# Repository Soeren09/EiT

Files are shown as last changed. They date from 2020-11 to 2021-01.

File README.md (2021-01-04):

# EiT
Practial project for Expert in Teams

# Folder structure
```bash
.Root
+-- Device_Tryouts
|   +-- # Contains Scene .xml file and collision setup
|   |
|   +-- components
|       +-- # Contains object files in .stl format
|
+-- PrototypeControl
|   +-- # Robot control
|
+-- STOMPA
|   +-- 3D Print
|   |   +-- # Contains all 3D printed components
|   +-- LaserCut
|   |   +-- # Containt all laser cutter drawings 
|   +-- PDF Work Drawings
|   |   +-- # Containt all Work Drawings for the mechanical components
|   +-- STOMPA 3D files
|       +-- # Containt the Invertor files for the CAD model
| 
+-- Workcell
|   +-- # Examplecode for RobworkStudio scene
|
+-- PluginUIapp
    +-- # Contain code for simulating the STOMPA in RobworkStudio
    
```

To rebuild the pluginUIapp.so:
Local paths are stored in: pluginUIapp/src/AbsolutePaths.h
which is ignored by git so you will have to create it. Mine looks like this:

#ifndef PLUGINUIAPP_ABSOLUTEPATHS_H
#define PLUGINUIAPP_ABSOLUTEPATHS_H
#include <string>

//Malte:
const std::string URFilePath = "/home/maltenj/EiT/Workcell/Scene.wc.xml";
const std::string GantryFilePath = "/home/maltenj/EiT/Device_Tryouts/STOMPAScene.xml";
const std::string PlaybackFilePath = "/home/maltenj/EiT/pluginUIapp/src/";
const char* GoogleLogPath =  "/home/maltenj/EiT/pluginUIapp/src/";

#endif

Insert your own paths. 

Also we linked ceres, so you might have to install it. see http://ceres-solver.org/
Alternatively you can delete all references to it. We don't use it currently. 

To build run:
$ cd /<PathToGit>/Eit/Practical/EiT/pluginUIapp/build
$ cmake ..
$ make -j4

And pray it links correctly...

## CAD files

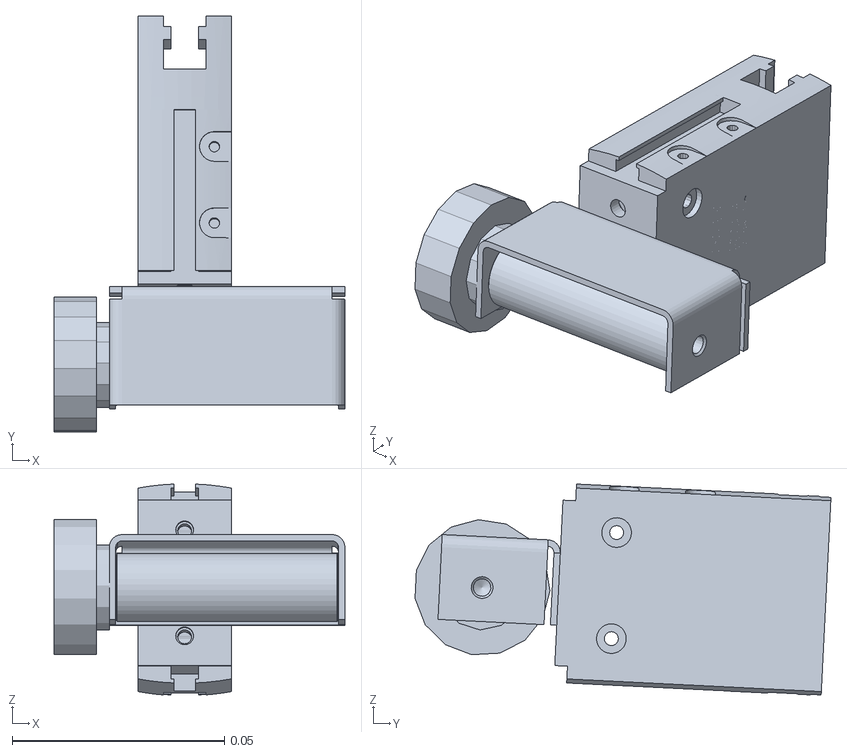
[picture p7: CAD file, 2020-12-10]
Device_Tryouts/components/test.stl
0.0685 x 0.098 x 0.0497

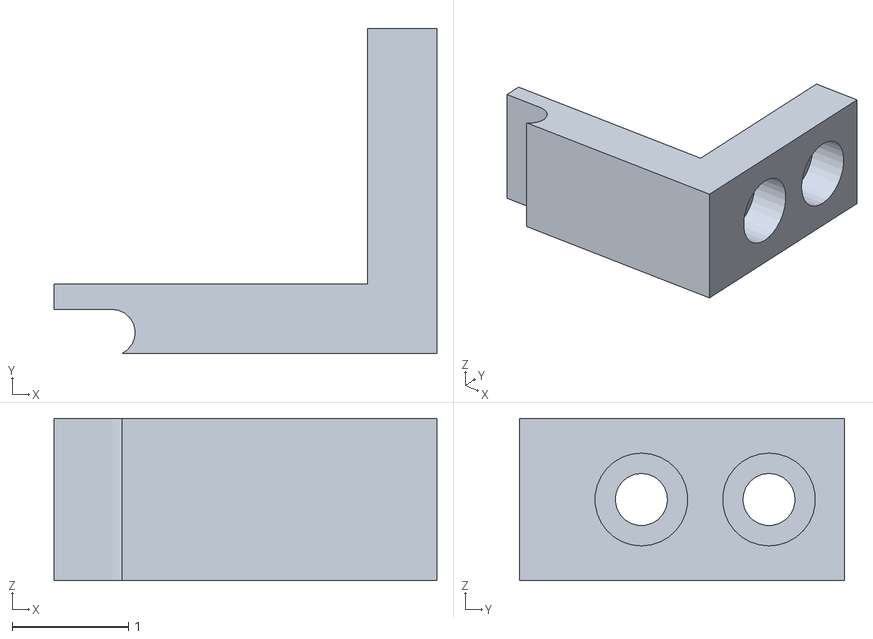
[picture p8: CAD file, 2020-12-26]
STOMPA/3Dprint/Gripper arm_extended2.stl
3.30 x 2.80 x 1.40

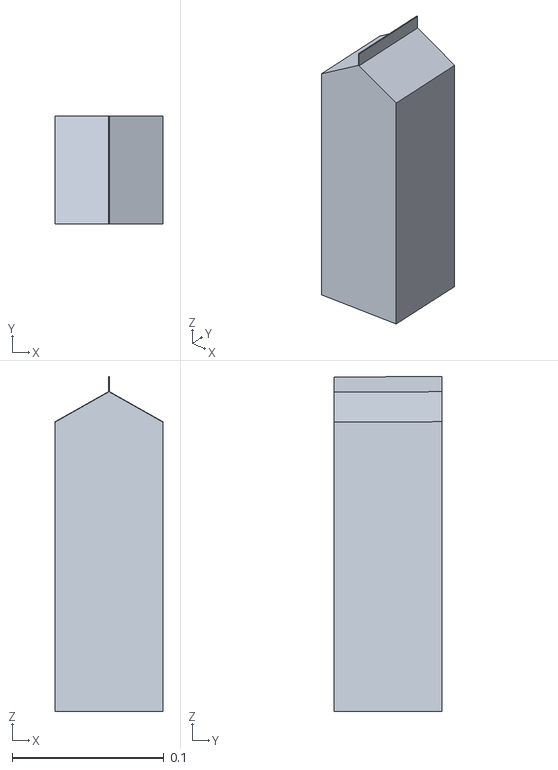
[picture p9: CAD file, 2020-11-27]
Workcell/parts/milk.obj
0.071 x 0.071 x 0.221

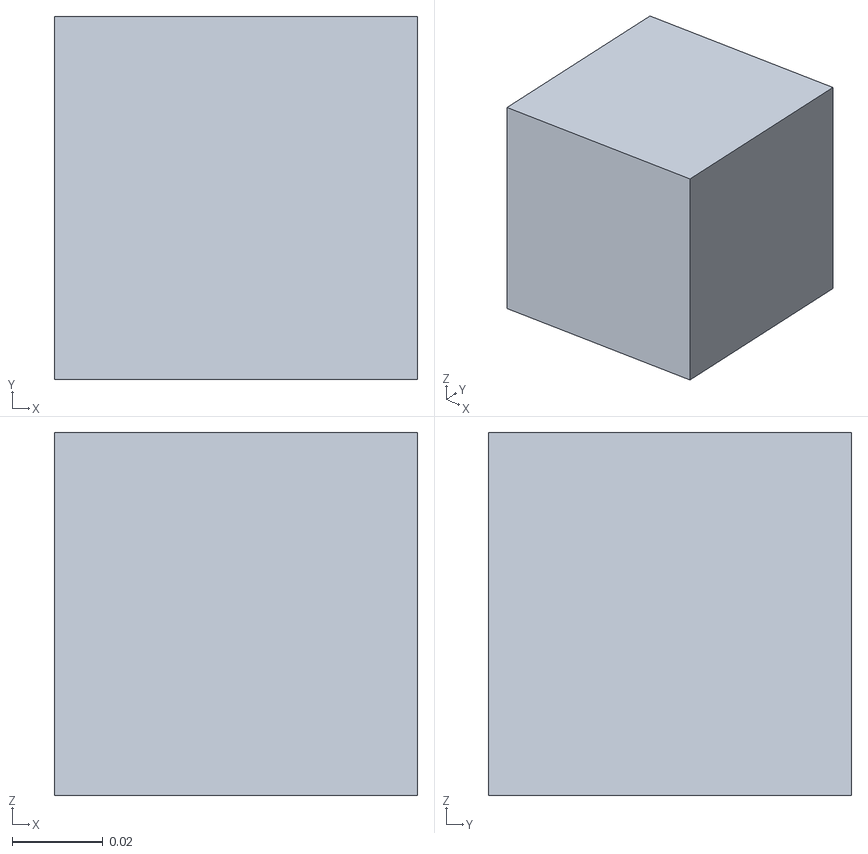
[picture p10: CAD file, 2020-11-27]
Workcell/parts/simpleObjects/square.stl
0.08 x 0.08 x 0.08

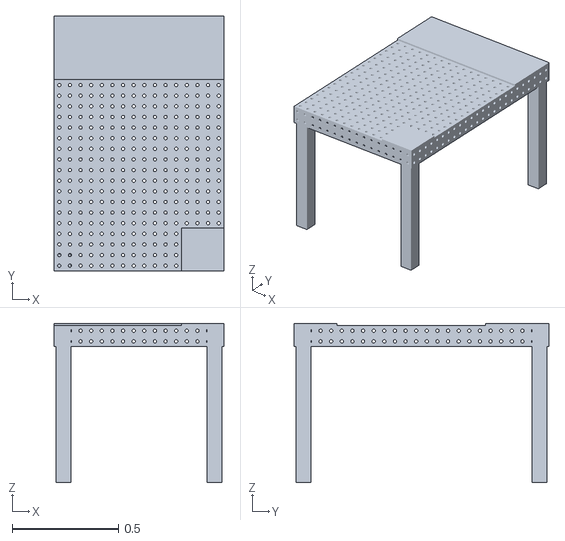
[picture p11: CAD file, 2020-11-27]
Workcell/table/Sigmund_table.stl
0.8 x 1.20 x 0.75

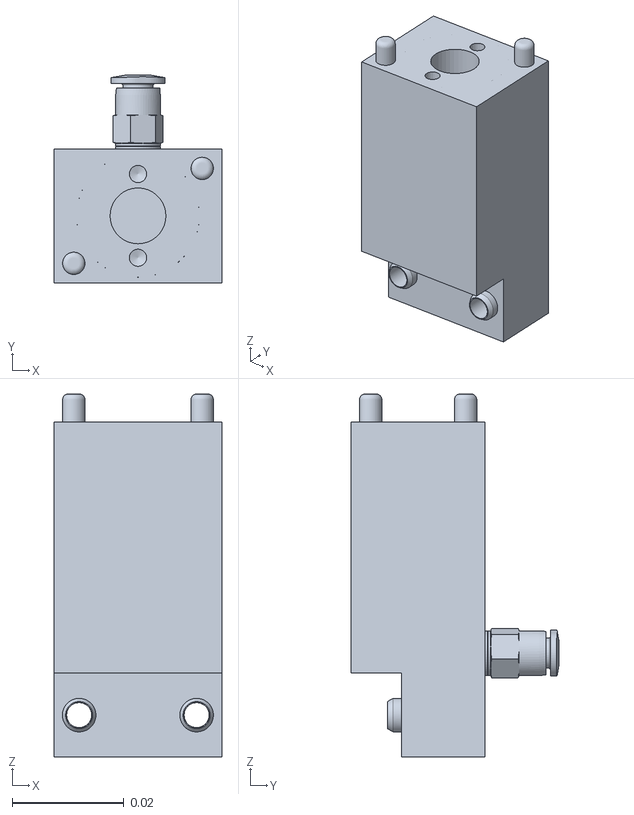
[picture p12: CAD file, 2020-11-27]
Workcell/wsg50/geometry/fingerexchange/Finger_exchanger.stl
0.03 x 0.0372 x 0.065

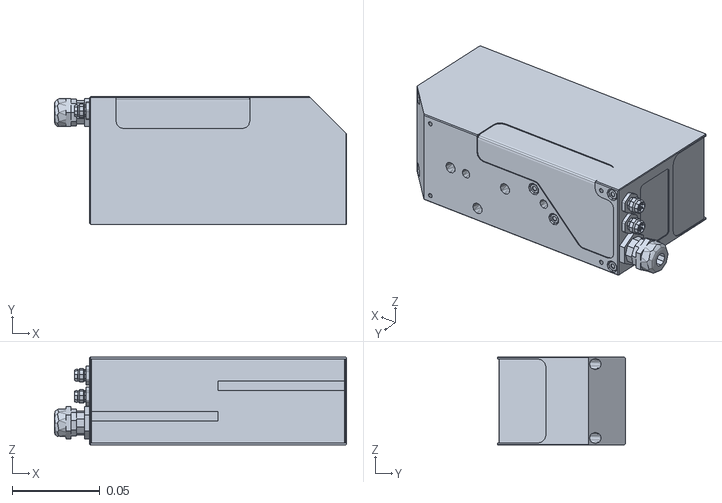
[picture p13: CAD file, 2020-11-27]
Workcell/wsg50/geometry/wsg50base.stl
0.166 x 0.0725 x 0.05

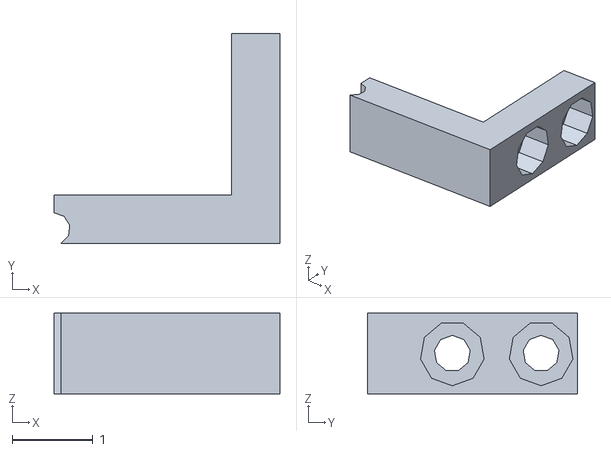
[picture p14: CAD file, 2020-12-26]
STOMPA/3Dprint/Gripper arm.stl
2.80 x 2.60 x 1.00

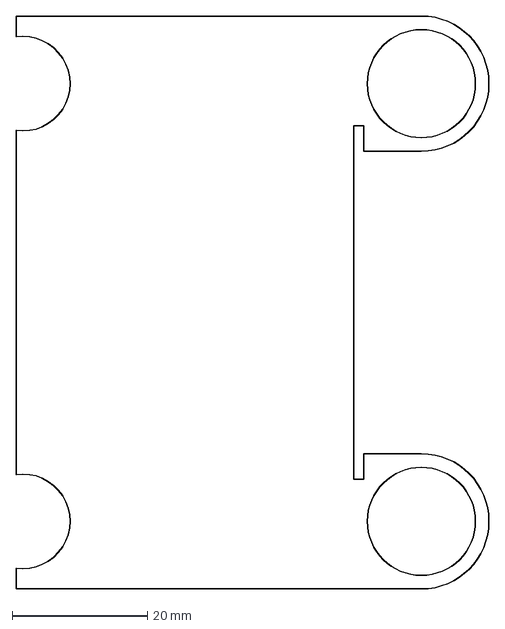
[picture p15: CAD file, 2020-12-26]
STOMPA/LaserCut/Laser cut 2 T 1,5.dxf
70.0 x 84.8 mm

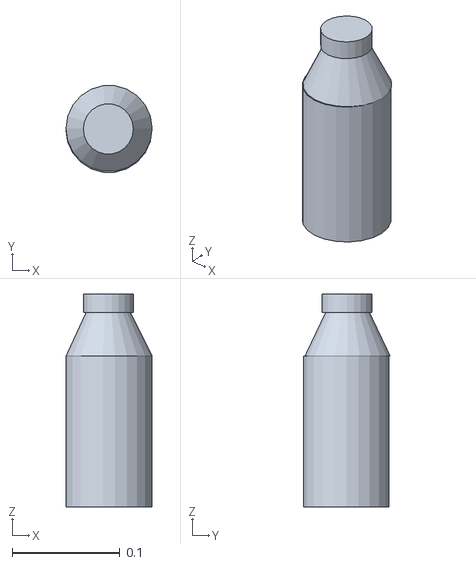
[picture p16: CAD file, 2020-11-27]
Workcell/parts/simpleObjects/bottle.stl
0.0801 x 0.0803 x 0.198

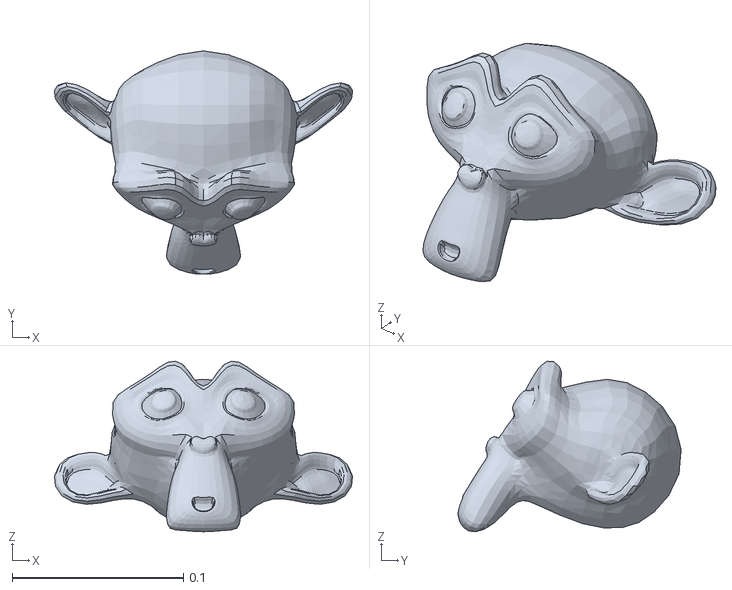
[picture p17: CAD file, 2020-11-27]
Workcell/parts/suzanne.obj
0.174 x 0.13 x 0.0997

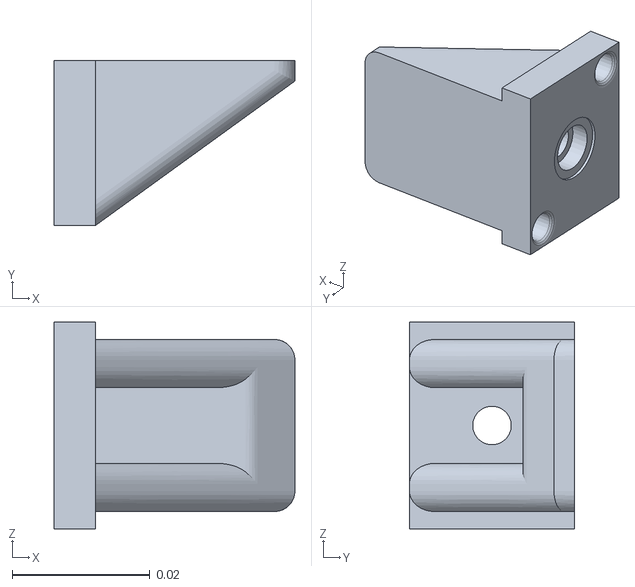
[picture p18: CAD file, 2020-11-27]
Workcell/wsg50/geometry/fingerexchange/Test_finger_tips.stl
0.035 x 0.024 x 0.03

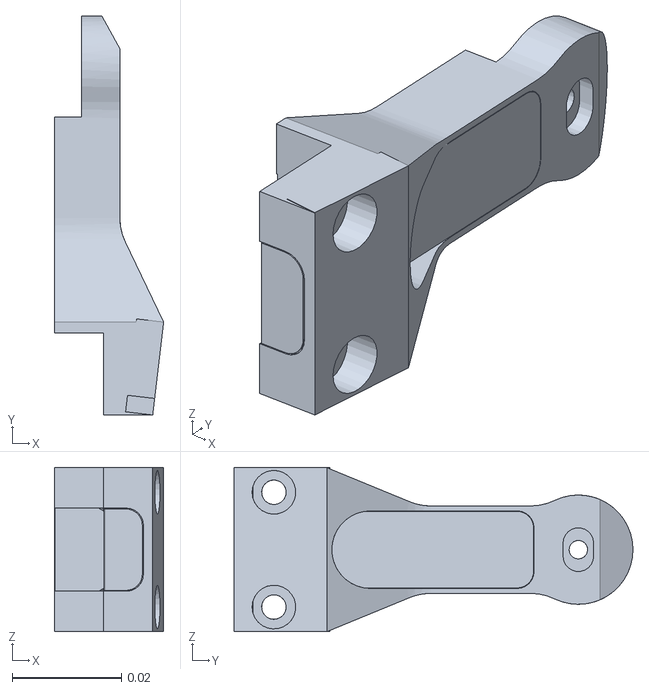
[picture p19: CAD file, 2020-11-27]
Workcell/wsg50/geometry/FingerWeiss50.stl
0.02 x 0.073 x 0.0301

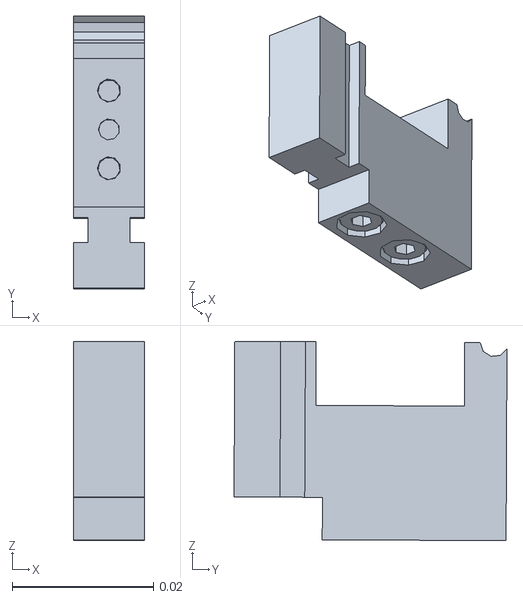
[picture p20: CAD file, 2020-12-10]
Device_Tryouts/components/stompa_finger_corrected.stl
0.01 x 0.0386 x 0.0282

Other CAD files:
STOMPA/LaserCut/Laser cutting 2.dwg
Device_Tryouts/components/stompa_arm2_corrected.stl
STOMPA/3Dprint/Gripper arm_extended1.stl
STOMPA/LaserCut/Laser cut 1 T 1,5.dxf
Workcell/wsg50/geometry/scale.scad
Device_Tryouts/components/gantry_extruder.stl
Device_Tryouts/components/gantry_x_modules.stl
Device_Tryouts/components/gantry_y_modules.stl
Device_Tryouts/components/gantry_z_modules.stl
Device_Tryouts/components/stompa_arm_1.stl
Device_Tryouts/components/stompa_arm_2.stl
Device_Tryouts/components/stompa_chassis.stl
Device_Tryouts/components/stompa_finger.stl
Device_Tryouts/components/stompa_magazine.stl
Device_Tryouts/components/stompa_rail.stl
Device_Tryouts/components/stompa_wheels.stl
Device_Tryouts/components/wall.stl
STOMPA/3Dprint/FanMount.stl
STOMPA/3Dprint/PCBBoard.ipt
STOMPA/3Dprint/PI3MK3M_Gripper arm.3mf
STOMPA/LaserCut/Laser cut 3 T 3.dxf
STOMPA/LaserCut/Laser cutting.dwg
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

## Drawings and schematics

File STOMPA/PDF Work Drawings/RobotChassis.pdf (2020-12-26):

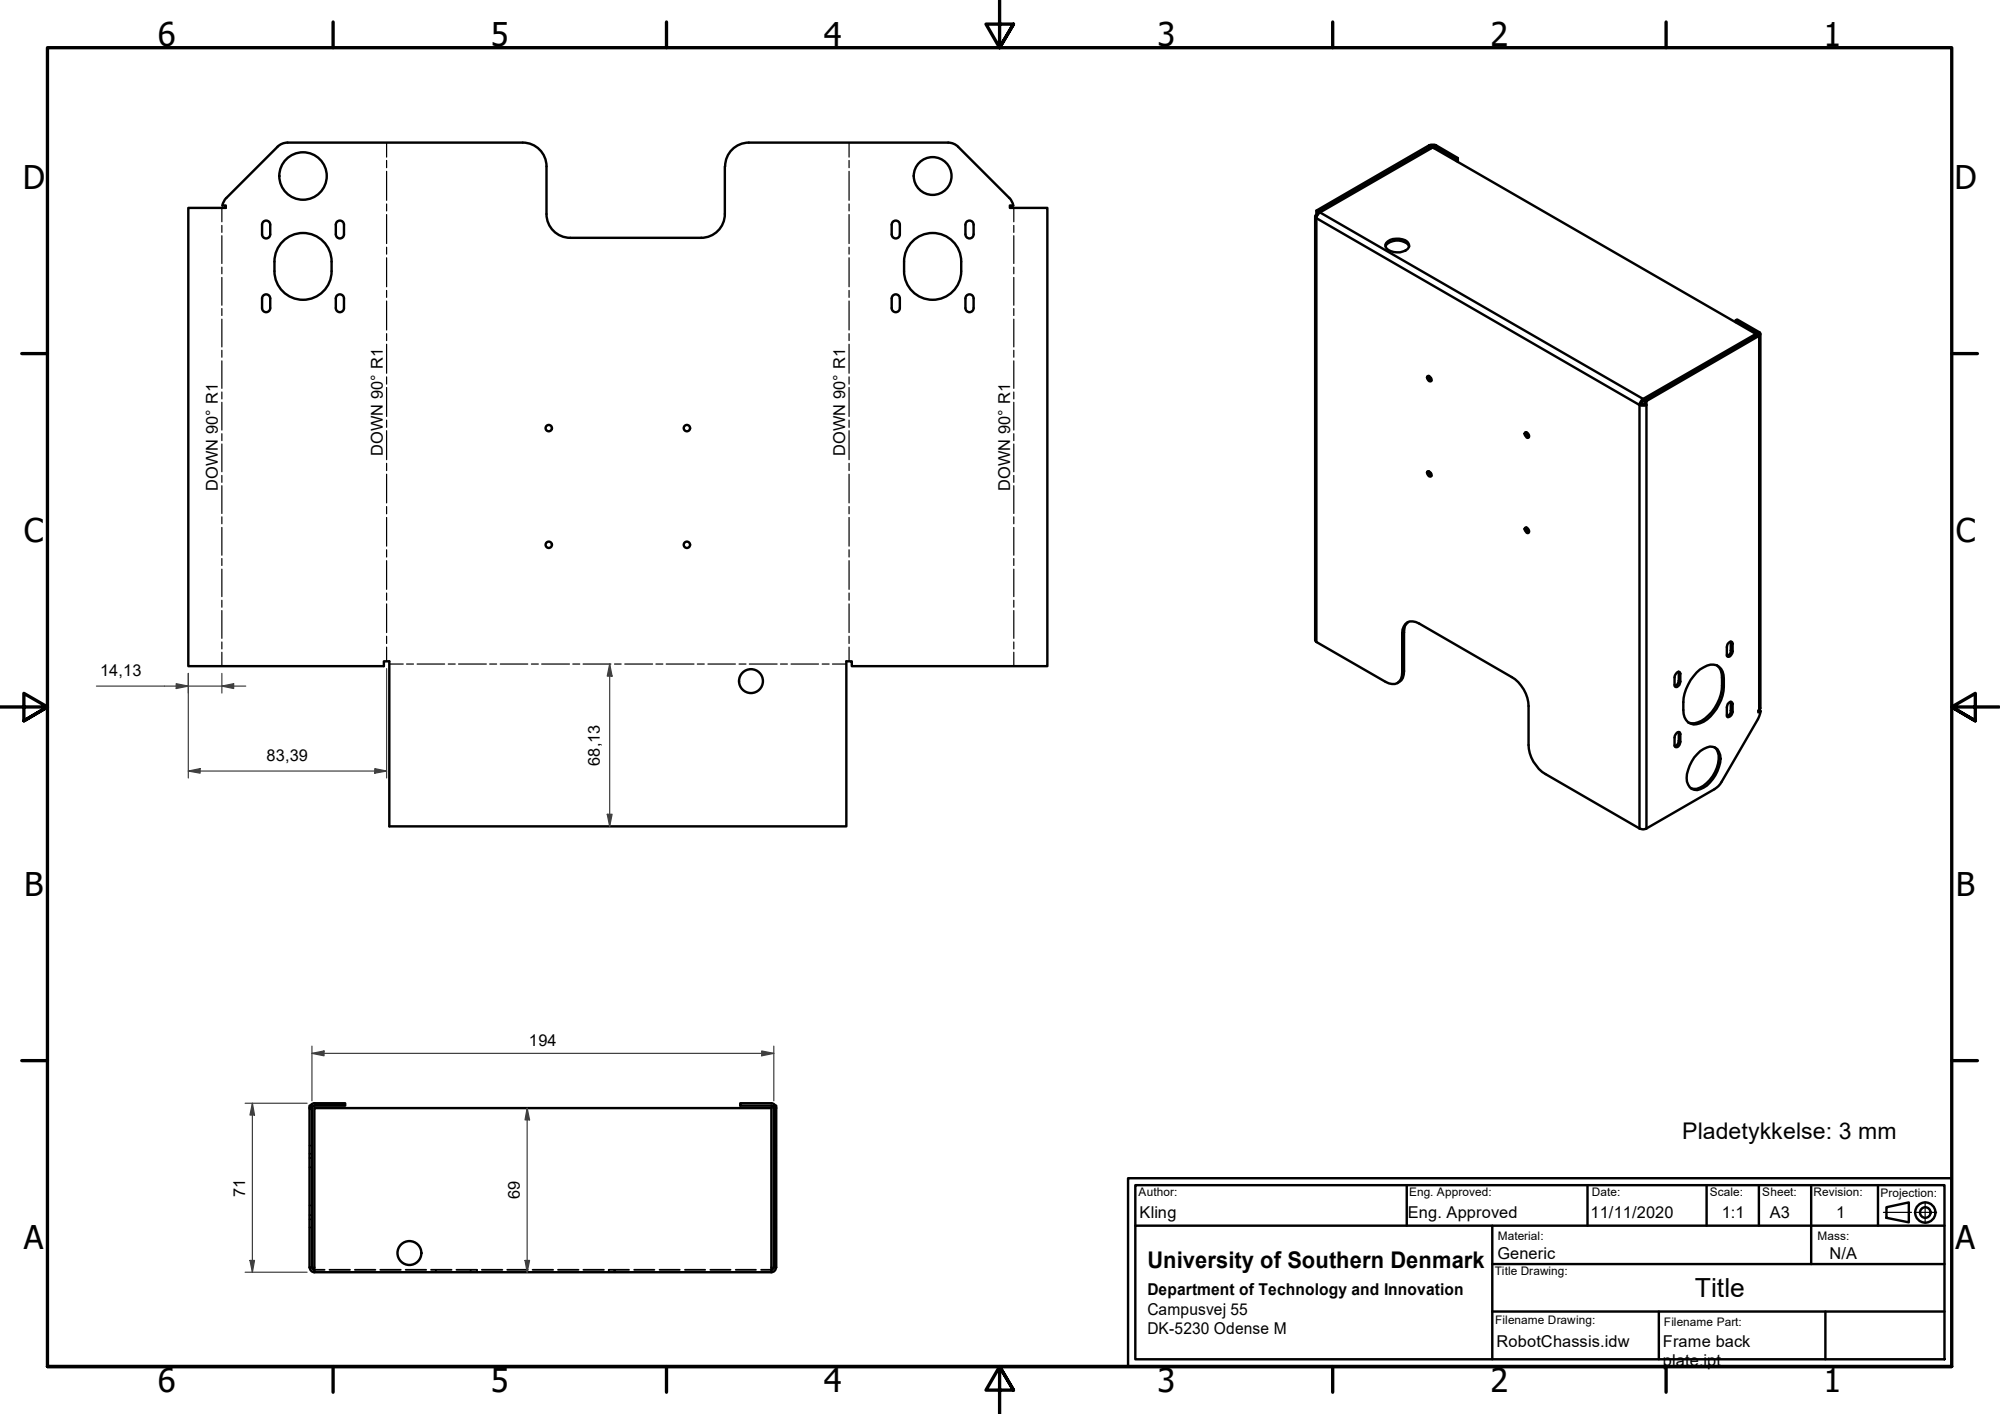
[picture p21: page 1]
Filename Drawing:; Title Drawing:; Filename Part: Frame back; Pladetykkelse: 3 mm

Author: Kling | Eng. Approved: Eng. Approved | Date: 11/11/2020 | Scale: 1:1 | Sheet: A3 | Revision: 1 | Projection:

University of Southern Denmark Department of Technology and Innovation Campusvej 55 DK-5230 Odense M | Material: Generic | Mass: N/A

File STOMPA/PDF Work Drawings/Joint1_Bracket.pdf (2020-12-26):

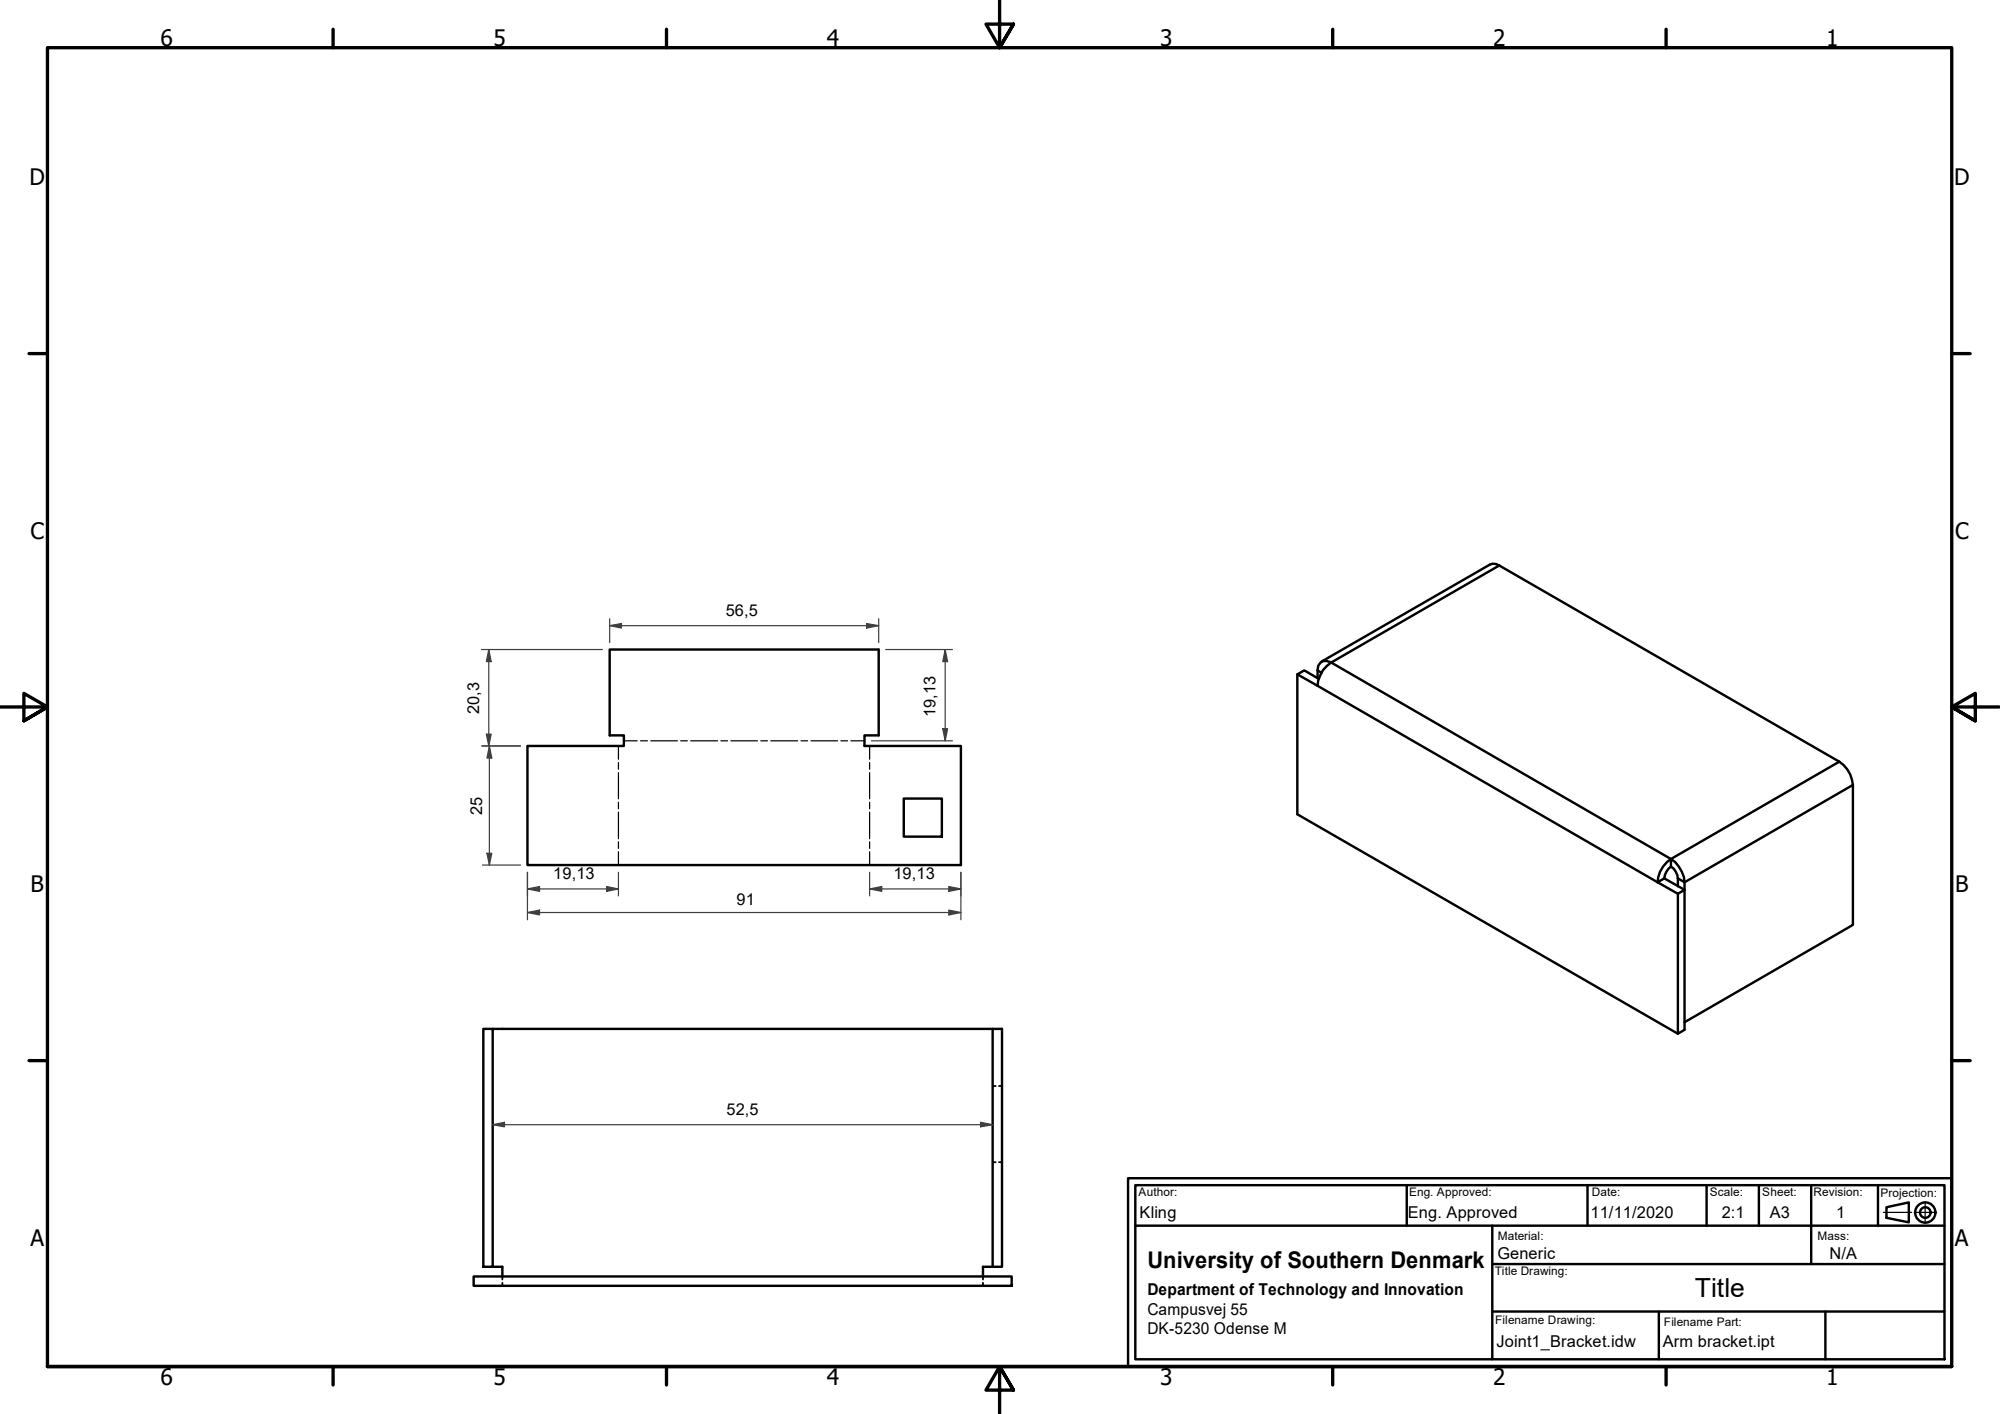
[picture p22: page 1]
Filename Drawing:; Title Drawing:

Author: Kling | Eng. Approved: Eng. Approved | Date: 11/11/2020 | Scale: 2:1 | Sheet: A3 | Revision: 1 | Projection:

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

Filename Part:
Arm bracket.ipt

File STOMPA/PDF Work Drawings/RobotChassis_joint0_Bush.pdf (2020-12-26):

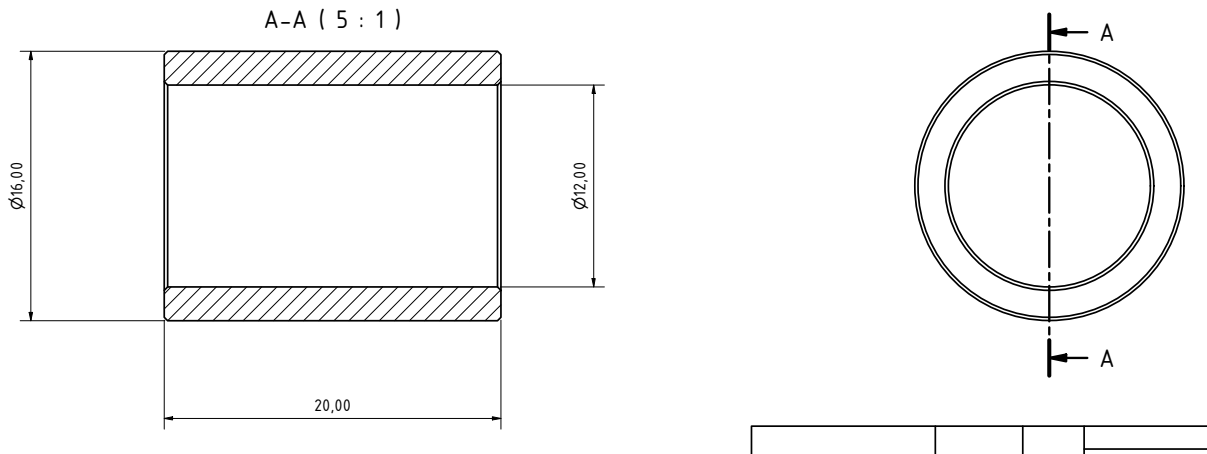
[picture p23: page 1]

Date | Name

Drawn | 16/11/2020 | Alfred Brauner

Checked

Standard

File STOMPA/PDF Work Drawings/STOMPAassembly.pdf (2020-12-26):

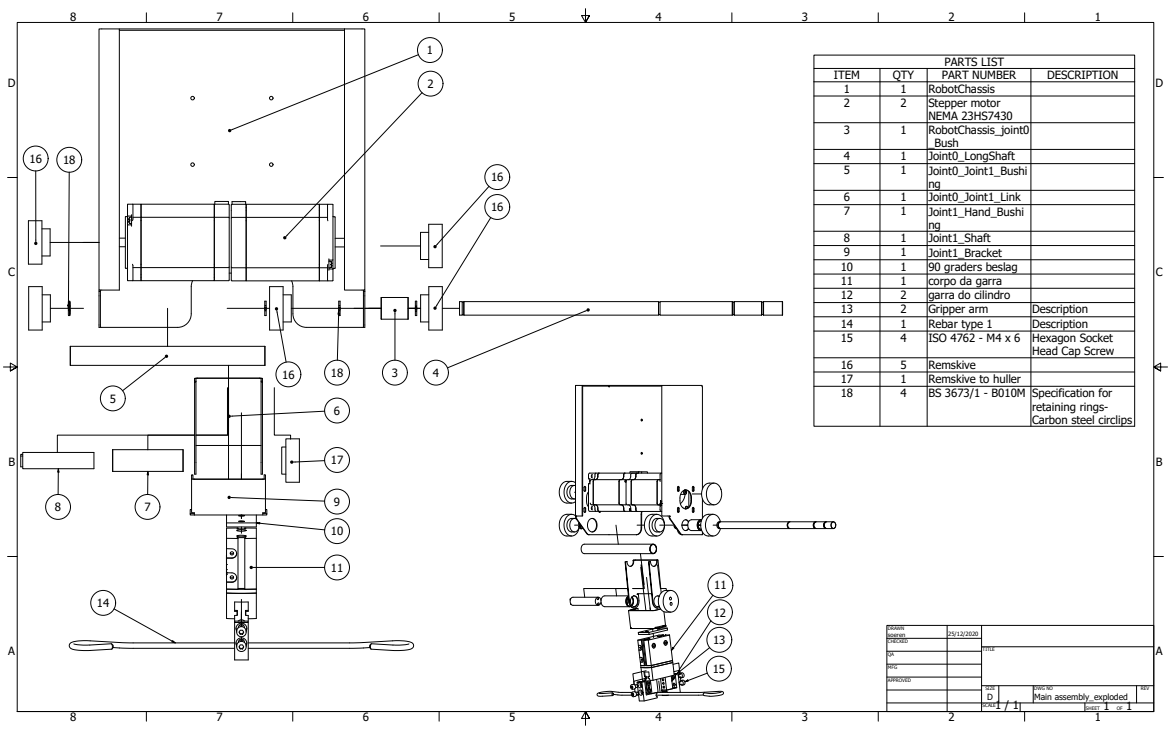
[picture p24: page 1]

I T E M | Q TY | P A RT N U M B E R | D E S C R I P T I O N
1 | 1 | R o b o t C h a s s i s
2 | 2 | S t e p p e r m o t o r N E M A 2 3 H S 7 4 3 0

4 | 1 | J o i n t 0 _ L o n g S h a ft
5 | 1 | J o i n t 0 _J o i n t 1 _ B u s h i n g

6 | 1 | J o i n t 0 _J o i n t 1 _ L i n k
7 | 1 | J o i n t 1 _ H a n d _ B u s h i n g

8 | 1 | J o i n t 1 _ S h a ft
9 | 1 | J o i n t 1 _ B r a c ke t
1 0 | 1 | 9 0 g r a d e r s b e sla g
1 1 | 1 | c o r p o d a g a r r a
1 2 | 2 | g a r r a d o c ili n d r o
1 3 | 2 | G r i p p e r a r m | D e s c r i p t i o n
1 4 | 1 | R e b a r ty p e 1 | D e s c r i p t i o n
1 5 | 4 | I S O 4 7 6 2 -M 4 x 6 | H e x a g o n S o c k e t H e a d C a p S c r e w

1 6 | 5 | R e m s k i v e
1 7 | 1 | R e m s k i v e t o h ulle r
1 8 | 4 | B S 3 6 7 3 / 1 -B 0 1 0 M | S p e c i f i c a t i o n fo r r e t a i n i n g r i n g s -C a r b o n s t e el c i r cli p s

S I Z E D | D W G N O M a i n a s s e m bly_ e x plo d e d | R E V

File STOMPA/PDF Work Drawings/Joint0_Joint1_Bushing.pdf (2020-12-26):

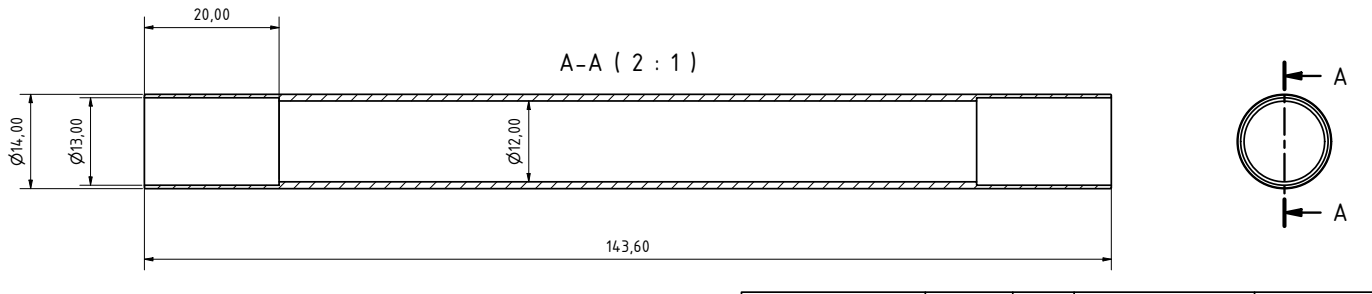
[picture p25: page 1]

Date | Name

Drawn | 16/11/2020 | Alfred Brauner

Checked

Standard

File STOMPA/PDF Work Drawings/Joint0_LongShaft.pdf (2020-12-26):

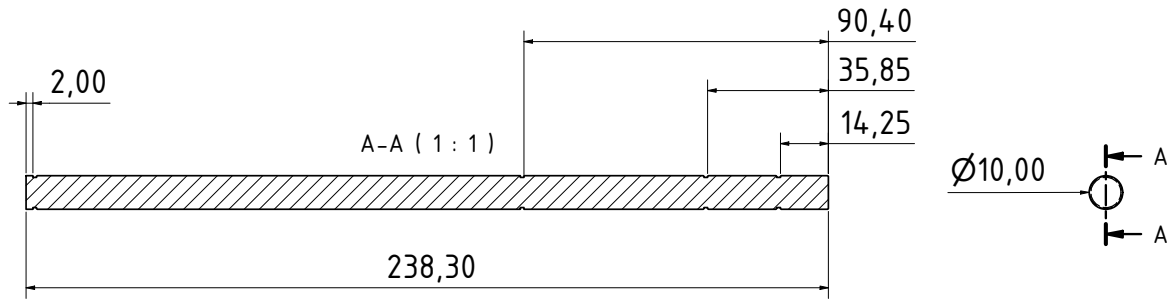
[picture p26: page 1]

Date | Name

Drawn | 16/11/2020 | Alfred Brauner

Checked

Standard

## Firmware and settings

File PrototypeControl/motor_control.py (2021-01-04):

from gpiozero import DigitalOutputDevice
from time import sleep
from random import choice
import math


class motor_control():
    def __init__(self):
        self.Motor_scaling = 2 # alternative 1

        self.ARM_CLOSE = 1
        self.ARM_OPEN = 0

        self.MOTOR_0 = 0
        self.MOTOR_1 = 1

        self.POS_ARM_0 = 0
        self.POS_ARM_1 = 0


        self.LIMIT_ARM_0 = [-(980)*self.Motor_scaling, 0] # Hard bound range 0-205 degrees (0-800 steps) - but is limited by arm1 config.
        self.LIMIT_ARM_1 = [0, 450*self.Motor_scaling]  # Total range 0-100 degrees - increases with current config of arm0

        # 400 steps = 90 degrees -> steps/degree = 4.44444444444
        
        self.deg_to_step = (400/90)*self.Motor_scaling
        self.degs_per_step = (90/400)*(1/self.Motor_scaling)

        self._dirs = [DigitalOutputDevice(20), DigitalOutputDevice(2)]
        self._steps = [DigitalOutputDevice(21), DigitalOutputDevice(3)]

        self.gripper_open = DigitalOutputDevice(10)

        # send to UR -> pin 11

        [d.off() for d in self._dirs]
        [s.off() for s in self._steps]


    def deg2step(self, deg):
	    return int(math.ceil(deg*self.deg_to_step))

    def set_direction(self, direction, motor):
        if direction == self.ARM_OPEN:
            if motor == self.MOTOR_0:
                self._dirs[0].on()
            else:
                self._dirs[1].off()
        else:
            if motor == self.MOTOR_0:
                self._dirs[0].off()
            else:
                self._dirs[1].on()
    
    def StepperMove(self, x=None, y=None, sleeptime=1/500):
        s_time=sleeptime/2
        if s_time < 1/16000:
            s_time = 1/16000
        move_y=False
        move_x=False
        if abs(x)> 1 or abs(y)> 1:
            print("Error - To high motor-step-value given - reduce step size or increase Frequency")
        # Update the legal bounds - both if x and/or y is given as input.
        if y==1:
            self.POS_ARM_1 += 1
            self.LIMIT_ARM_0[0] += 1
            self.LIMIT_ARM_0[1] += 1
            self.set_direction(self.ARM_OPEN, self.MOTOR_1)
            move_y = True  
        elif y==-1:
            self.POS_ARM_1 -= 1
            self.LIMIT_ARM_0[0] -= 1
            self.LIMIT_ARM_0[1] -= 1
            self.set_direction(self.ARM_CLOSE, self.MOTOR_1)
            move_y = True
        if x==1:
            self.POS_ARM_0 += 1
            self.LIMIT_ARM_1[0] += 1
            self.LIMIT_ARM_1[1] += 1
            self.set_direction(self.ARM_OPEN, self.MOTOR_0)
            move_x = True
        if x==-1:
            self.POS_ARM_0 -= 1
            self.LIMIT_ARM_1[0] -= 1
            self.LIMIT_ARM_1[1] -= 1
            self.set_direction(self.ARM_CLOSE, self.MOTOR_0)
            move_x = True

        # Check if arm 0 is withn legal bounds (clipped to be within hard-bounds)
        if self.POS_ARM_0 < max(self.LIMIT_ARM_0[0], 0): 
            self.POS_ARM_0 += 1
            self.LIMIT_ARM_1[0] += 1
            self.LIMIT_ARM_1[1] += 1
            print("ERROR - Arm 0 is out of bounds - lower.")
        elif self.POS_ARM_0 > min(self.LIMIT_ARM_0[1], (980)*self.Motor_scaling):
            self.POS_ARM_0 -= 1
            self.LIMIT_ARM_1[0] -= 1
            self.LIMIT_ARM_1[1] -= 1
            print("ERROR - Arm 0 is out of bounds - upper.")
        else:
            # If inside bounds - set arm 0 motor on.
            if move_x:
                self._steps[0].on()

        # Check if arm 1 is within the legal bounds
        if self.POS_ARM_1 < self.LIMIT_ARM_1[0]:
            self.POS_ARM_0 += 1
            self.LIMIT_ARM_1[0] += 1
            self.LIMIT_ARM_1[1] += 1
            print("ERROR - Arm 1 is out of bounds - lower.")
        elif self.POS_ARM_1 > self.LIMIT_ARM_1[1]:
            self.POS_ARM_1 -= 1
            self.LIMIT_ARM_0[0] -= 1
            self.LIMIT_ARM_0[1] -= 1
            print("ERROR - Arm 1 is out of bounds - upper.")
        else:
            # If inside bounds -  set arm 1 motor on
            if move_y:
                self._steps[1].on()

        # Sleep for half the duty cycle - turn off motors, and sleep for rest of duty cycle.
        sleep(s_time)
        self._steps[0].off()
        self._steps[1].off()
        sleep(s_time)

    def print_status(self):
        print(f'Current config: ({self.POS_ARM_0}, {self.POS_ARM_1}). Arm_0 limits: {self.LIMIT_ARM_0}. Arm_1 limits: {self.LIMIT_ARM_1}.')

    def get_pose(self, decoupled=False, degrees=True):
        if degrees:
            conv = self.degs_per_step
        else:
            conv = 1
        if decoupled:
            return [self.POS_ARM_0*conv, self.POS_ARM_1*conv-self.POS_ARM_0*conv]
        else:
            return [self.POS_ARM_0*conv, self.POS_ARM_1*conv]

if __name__ == "__main__":
    tester = motor_control()
    tester.StepperMove(x=0, y=1)
    tester.print_status()
    tester.StepperMove(x=0, y=1)
    tester.print_status()
    tester.StepperMove(x=0, y=1)
    tester.print_status()
    tester.StepperMove(x=-1, y=0)
    tester.print_status()
    tester.StepperMove(x=-1, y=0)
    tester.print_status()
    tester.StepperMove(x=-1, y=0)
    tester.print_status()

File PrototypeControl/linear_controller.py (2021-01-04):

from gpiozero import DigitalInputDevice
from motor_control import motor_control
import kinematics
import time

motor = motor_control()
UR_signal = DigitalInputDevice(9)

#a = 1 / 8
#deg_per_step = 1.8 * a
# complete joint limits - (0-220 degrees), (joint 1 values + (0-90 degrees))

def moveQ(q_end_in, duration, frequency=8000, verbose : bool = False):
	n = int(duration * frequency)
	t_start = time.time()

	q_start = motor.get_pose()
	q_end = [q_end_in[0], q_end_in[0]+q_end_in[1]]

	qs = []
	for i in range(n + 1):
		t = i / n
		q_deg = [(q2 * t + q1 * (1 - t)) for q1, q2 in zip(q_start, q_end)]
		q_step = [int(q / motor.degs_per_step) for q in q_deg]
		qs.append(q_step)

	qs_changes = [(i / frequency, [q2 - q1 for q1, q2 in zip(qs[i], qs[i + 1])]) for i in range(n)]
	qs_changes = [(t, [d1, d2]) for t, (d1, d2) in qs_changes if (d1 != 0 or d2 != 0)]

	for t, (d1, d2) in qs_changes:
		if verbose:
			print(f"{t:0.2f}s: {d1}, {d2}")
		dt = time.time() - t_start
		motor.StepperMove(d1, d2, t - dt)

def MoveL(start,end,steps,time):
	kin = kinematics.kinematics(L1=0.055,L2=0.105,offset=-17)
	# Metoden nedenfor laver en list af Q-values, som skal afspilles med jævn fart, så burde C-space linear movement opnåes.
	LinPath = kinematics.LinDecomp(start,end,steps)
	for Qs in range(len(LinPath)):
		moveQ(LinPath[Qs],time/steps,8000)

# ----------------- TESTS AND DEMONSTRATIONS BELOW ----------------------------

def test_of_decoupled_joints():
	# test with joint decoupling:
	moveQ([107.5, 0], 2)
	motor.print_status()
	print(motor.get_pose(decoupled=True))
	time.sleep(0.5)
	moveQ([0, 0], 2)
	moveQ([107, 0], 2)
	motor.print_status()
	print(motor.get_pose(decoupled=True))
	time.sleep(0.5)
	moveQ([0, 0], 2)

# Can be used for demonstration in case linear motion fails. -> only uses moveQ commands
def circularMove(use_gripper=True):
	# Complete Circular move routine. the time.sleep(1.60) should be replaced with wait until signal from UR
	while True:
		moveQ([0,88],0.75, 8000) #WP 1 - Curl ind, så man ikke rammer muren
		question = input("Enter to continue with circularMove. input \'x\' to quit. \n")
		if question == 'x':
			break
		for i in range(3):
			moveQ([207,88],1.0, 8000) #WP 2 - entry point til pick up rebar
			if use_gripper:
				motor.gripper_open.on() # gør gripper klar til at tage en rebar
			moveQ([220,75],0.5, 8000) #WP 3 - rebar pickup point
			if use_gripper:
				motor.gripper_open.off() # luk gripper for at holde rebar
			while not UR_signal.is_active:
				pass 
			time.sleep(0.3)
			moveQ([97.64,52.8],0.25, 8000) #WP - Entry point til placement
			moveQ([68,52.8],0.25, 8000) #WP - Let go of rebar
			if use_gripper:
				motor.gripper_open.on() # åben gripper for at slippe rebar
			moveQ([38.36,52.8],0.25, 8000) #WP - End of placement point
			if use_gripper:
				motor.gripper_open.off() # luk gripper igen...
			moveQ([0,0],0.55, 8000)  # gør igen klar til at curle up
			moveQ([0,88],0.55, 8000)

	moveQ([0,0],0.75, 8000) # sætter roboten i home til sidst, såfremt while loopet brydes

def testMoveL():
	moveQ([0,88],0.75, 8000) #WP 1 - Curl ind, så man ikke rammer muren
	kin = kinematics.kinematics(L1=0.055,L2=0.105,offset=-17)
	#brug forward kinematics for at sikre at startpunkt er identisk med nuværende punkt.
	startPosition = kin.forward(motor.get_pose(decoupled=True,degrees=True))
	endPosition = [0.09,0.121]
	moveL(startPosition,endPosition,steps=1000,time=1.2)
	moveQ([0,0],0.75, 8000) # sætter roboten i home til sidst

# Bruges til demonstrationen. I dette tilfælde har vi ikke brugt Forward kinematics som startpunkt i LinDecomp funktionen.
def linearMove(depth=0.143, length=0.12, steps=1000, letGoStep=450, use_gripper=False):
	kin = kinematics.kinematics(L1=0.055,L2=0.105,offset=-17)
	# Metoden nedenfor laver en list af Q-values, som skal afspilles med jævn fart, så burde C-space linear movement opnåes.
	LinPath = kinematics.LinDecomp([-length/2, depth],[length/2, depth-0.005],steps)
	EntryPath = kin.invers(-length/2, depth-0.001)
	ExitPath = kin.invers(length/2, depth-0.015)
	count=0
	while True:
		moveQ([0,88],0.75, 8000) #WP 1 - Curl ind, så man ikke rammer muren
		count+=1
		if count > 5:
			break
		print(count)
		for i in range(1):
			moveQ([207,88],1.0, 8000) #WP 2 - entry point til pick up rebar
			if use_gripper:
				motor.gripper_open.on() # gør gripper klar til at tage en rebar
			moveQ([220,75],0.5, 8000) #WP 3 - rebar pickup point
			if use_gripper:
				motor.gripper_open.off() # luk gripper for at holde rebar
				closed=True
			while not UR_signal.is_active:
				pass 
			time.sleep(0.3)
			moveQ(EntryPath,0.25,8000)
			for Qs in range(len(LinPath)):
				moveQ(LinPath[Qs],0.0005,80000)
				if use_gripper and Qs > letGoStep and closed==True:
					motor.gripper_open.on()
					closed=False
			moveQ(ExitPath,0.5, 8000)
			if use_gripper:
				motor.gripper_open.off()
				closed=True
			moveQ([0,0],0.55, 8000)  # gør igen klar til at curle up
			moveQ([0,88],0.55, 8000)
	
	moveQ([0,0],0.75, 8000) # sætter roboten i home til sidst, såfremt while loopet brydes

# Backup:
# circularMove(use_gripper=True)

# Primary show:
# depth = push depth, length = length of linear motion, steps = number of steps the linear motion is divided into, legGoStep = step number when the gripper lets go.
linearMove(depth=0.146, length=0.12, steps=800, letGoStep=300, use_gripper=True)

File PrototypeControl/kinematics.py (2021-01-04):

import math
import kinematics

class kinematics:
    def __init__(self, L1, L2, offset):
        self._L1 = L1
        self._L2 = L2
        self._offset = math.radians(offset)

    def forward(self, q1_degs, q2_degs):
        q1 = math.radians(q1_degs)
        q2 = math.radians(q2_degs)
        x = self._L1*math.cos(self._offset + q1) + self._L2*(math.cos(self._offset + q1)*math.cos(q2) - math.sin(self._offset + q1)*math.sin(q2))
        y = self._L1*math.sin(self._offset + q1) + self._L2*(math.cos(self._offset + q1)*math.sin(q2) + math.sin(self._offset + q1)*math.cos(q2))
        return x, y

    def invers(self, x,y):
        cos_q2 = (x*x + y*y - self._L1*self._L1  - self._L2*self._L2 ) /(2*self._L1*self._L2)
        q2 = math.acos(cos_q2)
        q1 = math.atan2(y,x)-math.atan2((self._L2*math.sin(q2)),(self._L1+self._L2*cos_q2) )
        q1_out = math.degrees(q1-self._offset)
        q2_out = math.degrees(q2)
        return q1_out, q2_out

def LinDecomp(start, end, steps):
    kin = kinematics(L1=0.055,L2=0.105,offset=-17)
    output=[]
    for i in range(steps):
        step = (1+i)/steps
        x = start[0]+((end[0]-start[0])*step)
        y = start[1]+((end[1]-start[1])*step)
        q1,q2 = kin.invers(x,y)
        if q1 < 0 or q1 > 215 or q2 < 0 or q2 > 90:
            print("Error - inv kin solution is out of bounds")
        output.append([q1,q2])
    return output


if __name__ == "__main__":
    # Tests of forward and invers kinematics.
    kin = kinematics(L1=0.055,L2=0.105,offset=-17)
    x,y = kin.forward(67,40)
    print(x, y)
    q1,q2 = kin.invers(x,y)
    print(q1,q2)
    # Metoden nedenfor laver en list af Q-values, som skal afspilles med jævn fart, så burde C-space linear movement opnåes.
    out = LinDecomp([0.06, 0.143],[-0.06, 0.143],100)

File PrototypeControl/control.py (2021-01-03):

from gpiozero import DigitalOutputDevice
from time import sleep
from random import choice
import math


ARM_CLOSE = 1
ARM_OPEN = 0

MOTOR_0 = 0
MOTOR_1 = 1

POS_ARM_0 = 0
POS_ARM_1 = 0


# Elbow 400 steps = 90 degree   400/90 (step/degree) = 4.44444444444      degree/step 400

dirs = [DigitalOutputDevice(20), DigitalOutputDevice(2)]
steps = [DigitalOutputDevice(21), DigitalOutputDevice(3)]

[d.off() for d in dirs]
[s.off() for s in steps]


def deg2step(DEG):
	return int(math.ceil(DEG*4.44444444444))


''' Direction off:
0: arms closes (towards starting position)
1: Arm opens '''
def direction(DIRECTION):
	if DIRECTION:
		dirs[0].on()
		dirs[1].off()
	else:
		dirs[0].off()
		dirs[1].on()


def powerMoter(motor, DIRECTION, speed=1000):
	direction(DIRECTION)
	pulse_time = 1/speed
	if motor == 0: # Shoulder movement
		steps[0].on()
		steps[1].on()
		sleep(pulse_time)
		steps[0].off()
		steps[1].off()
		sleep(pulse_time)
	
	else:	  # Elbow Movement
		steps[motor].on()
		sleep(pulse_time)
		steps[motor].off()
		sleep(pulse_time)


def moveToPos(POSE):

#	if POSE[0] = POS_ARM0 and POSE = POS_ARM1: # Already at the correct position

#	if POSE[]


	# POS_ARM_0
	# POS_ARM_1


#motor = 0
#direction = 1 # 0 is forward
#duration = 0.001



	for i in range(deg2step(90)):
		powerMoter(MOTOR_1, ARM_OPEN)
		POS_ARM_0+=1

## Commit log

2020-11-27 Shell for gantry + UR is setup
2020-12-03 building scene
    [base.stl, gantry_extruder.stl, gantry_x_modules.stl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]
2020-12-09 added correct joint limits to total.xml
2020-12-10 total.xml v1.0
    [stompa_arm2_corrected.stl, stompa_finger_corrected.stl, test.stl]
2020-12-26 Add files via upload
    STOMPA 3D drawings and Working Drawings added
    [2 PRINT.0002.idw, 90 graders beslag.ipt, Arm Assembly.0011.iam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]
2021-01-04 Final corrections to prototype code
    [control.py, gripper.py, kinematics.py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]
